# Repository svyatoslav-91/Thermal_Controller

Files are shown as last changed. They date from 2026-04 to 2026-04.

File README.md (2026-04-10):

Разработанное устройство (включая всю требуемую документацию согласно ЕСКД) — ПИД-регулятор контроля температуры печи оплавления с программируемым термопрофилем. 
Устройство снабжено преобразователем напряжения, подключающимся к бытовой электрической сети 230 В. Преобразователь питания снабжает энергией как цифровую часть устройства управления, так и аналоговую часть нагревательного устройства и устройства контроля температуры. 
Устройство имеет интерфейс взаимодействия с пользователем (ЖК-дисплей и клавиатурную панель). Также разработано ПО для управления, настройки и тестирования устройства с ПК на языке С. 
Цифровая часть управления реализована на микроконтроллере с ARM-архитектурой STM32F411CEU6 — микроконтроллер, 32-бит, Cortex-M4, 100 МГц, 512 КБ Flash, 128 КБ SRAM, 36 I/O [UFQFPN-48_7x7]. 
Аналоговые устройства взаимодействия с нагревательным элементом гальванически развязаны. Термопара в связке с MAX6675ISA по SPI передает данные о температуре в МК, который с помощью ПИД регуляции вычисляет необходимое время включения нагревателя в окне регулирования. 
Коммутирование нагревателя осуществляюется с помощью SSR реле что обеспечивает полную гальваническую развязку от цепи 220 В нагревателя, а также быстрый отклик.

По ссылке на видео размещена демонстрация работы устройства: программирование термопрофиля, запуск ПИД-регулятора, отображение температуры на ЖК-дисплее и в ПО на ПК, а также реакция системы на изменение уставки, запуск различных термопрофилей и запись во flash. (в качестве нагревателя для удобства используется лампочка накаливания).
(https://rutube.ru/video/9960f83b43a8872c07baa9010c9fd1d7/)

В корневой папке проекта можно найти:

принципиальные электрические схемы (в форматах PDFисходники для Altium Designer);

Gerber-файлы для изготовления печатной платы;

сборочные чертежи платы и корпуса (в форматах PDF);

спецификации компонентов (ВП, ПЭ3)(в форматах PDF);

3D-модель печатной платы (Step) для проверки совместимости с корпусом и механической интеграции;

исходные коды встроенного ПО для STM32F411CEU6 (с проектом для Keil);

исходный код ПО для ПК на языке C;

Вся конструкторская документация оформлена по стандартам ЕСКД (схемы, чертежи, спецификации, пояснительная записка). Проект полностью готов к серийному производству и может быть воспроизведён по предоставленным материалам.

В release-пакет включены:

исполняемый файл приложения для ПК (Windows) для управления, настройки и тестирования устройства;

краткое руководство пользователя (Release Notes).

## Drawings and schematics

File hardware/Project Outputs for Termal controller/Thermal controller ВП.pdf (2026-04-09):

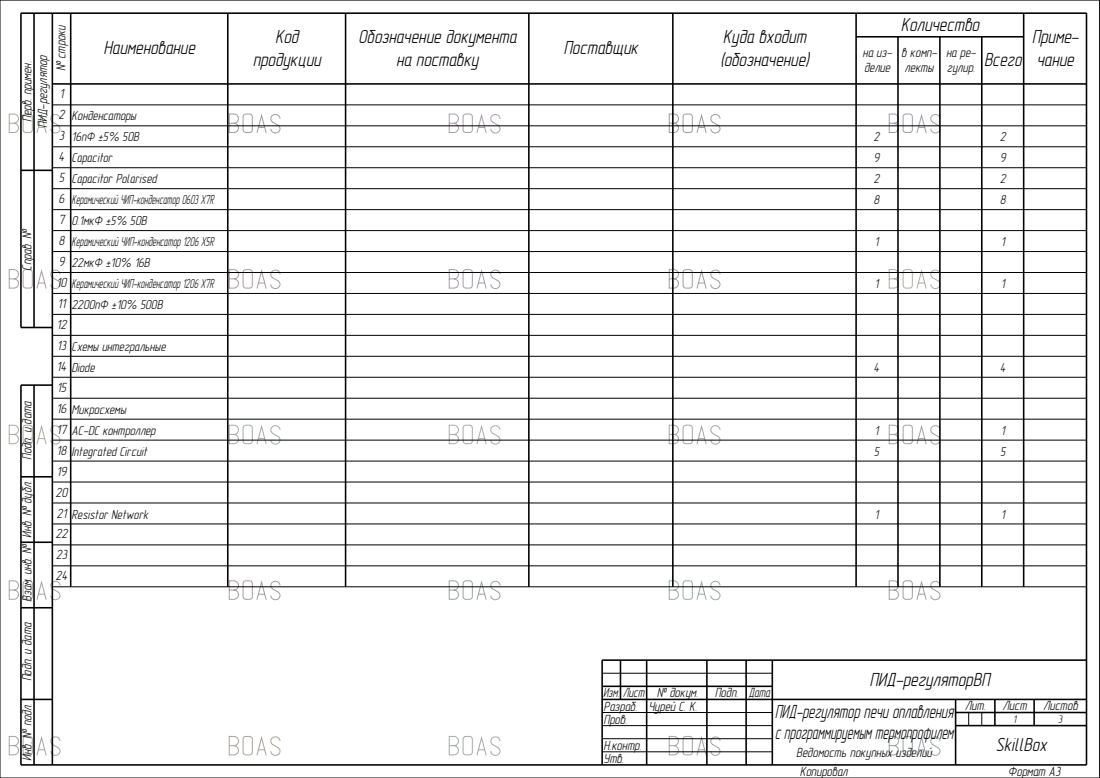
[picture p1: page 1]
Лит.; Копировал; Разраб. Пров.; Лист; Листов; Формат А3; Чурей С. К.; Ведомость покупных изделий; SkillBox; ПИД-регулятор

№ строки Наименование Код продукции Обозначение документа на поставку Поставщик Куда входит (обозначение) Количество на из- делие в комп- лекты на ре- гулир. Всего Приме- чание

Перв. примен. Справ. № Подп. и дата Инв. № дубл. Взам. инв. № Подп. и дата Инв. № подл.

2 | Конденсаторы
3 | 16пФ ±5% 50В | 2 | 2
4 | Capacitor | 9 | 9
5 | Capacitor Polarised | 2 | 2
6 | Керамический ЧИП-конденсатор 0603 X7R | 8 | 8
7 | 0.1мкФ ±5% 50В
8 | Керамический ЧИП-конденсатор 1206 X5R | 1 | 1
9 | 22мкФ ±10% 16В
10 | Керамический ЧИП-конденсатор 1206 X7R | 1 | 1
11 | 2200пФ ±10% 500В
12
13 | Схемы интегральные
14 | Diode | 4 | 4
15
16 | Микросхемы
17 | AC-DC контроллер | 1 | 1
18 | Integrated Circuit | 5 | 5
19
20
21 | Resistor Network | 1 | 1
22
23
24

ПИД-регуляторВП

Изм. Лист | № докум. | Подп. | Дата

ПИД-регулятор печи оплавления
с программируемым термопрофилем

Н.контр.
Утв.

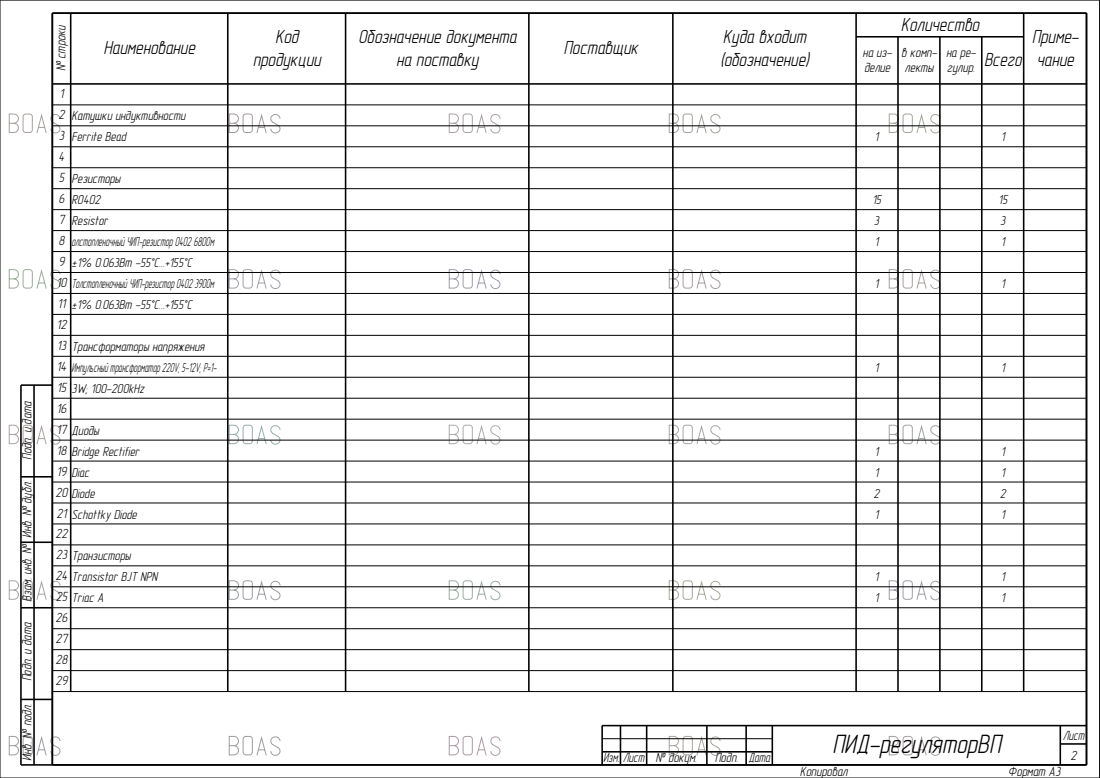
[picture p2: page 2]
Изм. Лист; № докум.; Подп.; Дата; Лист; ПИД-регуляторВП

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

2 | Катушки индуктивности
3 | Ferrite Bead | | 1 | 1
5 | Резисторы
6 | R0402 | | 15 | 15
7 | Resistor | | 3 | 3
8 | олстопленочный ЧИП-резистор 0402 680Ом | | 1 | 1
9 | ±1% 0.063Вт -55°С...+155°С
10 | Толстопленочный ЧИП-резистор 0402 390Ом | | 1 | 1
11 | ±1% 0.063Вт -55°С...+155°С
12
13 | Трансформаторы напряжения
14 | Импульсный трансформатор 220V; 5-12V; P=1- | | 1 | 1
15 | 3W; 100-200kHz
16
17 | Диоды
18 | Bridge Rectifier | | 1 | 1
19 | Diac | | 1 | 1
20 | Diode | | 2 | 2
21 | Schottky Diode | | 1 | 1
22
23 | Транзисторы
24 | Transistor BJT NPN | | 1 | 1
25 | Triac A | | 1 | 1
26
27
28
29

Подп. и дата Инв. № дубл. Взам. инв. № Подп. и дата Инв. № подл.

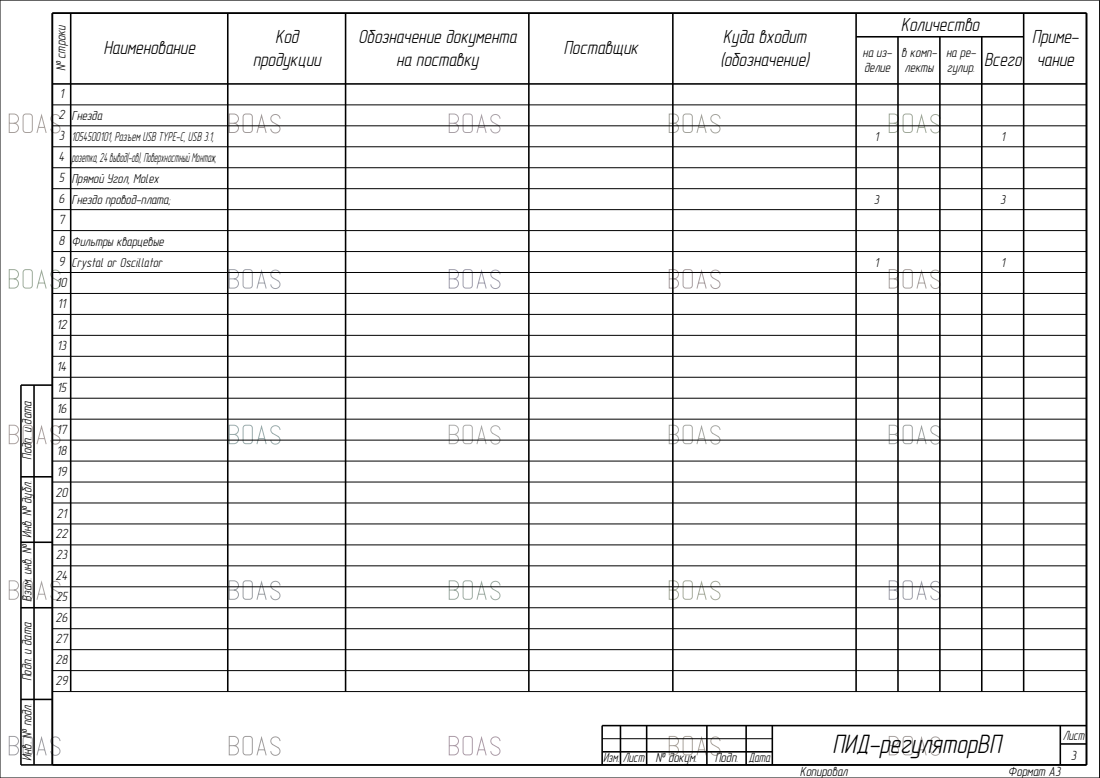
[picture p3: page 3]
Изм. Лист; № докум.; Подп.; Дата; Лист; ПИД-регуляторВП

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

2 | Гнезда
3 | 1054500101, Разъем USB TYPE-C, USB 3.1, | | 1 | 1
4 | розетка, 24 вывод(-ов), Поверхностный Монтаж,
5 | Прямой Угол, Molex
6 | Гнездо провод-плата; | | 3 | 3
8 | Фильтры кварцевые
9 | Crystal or Oscillator | | 1 | 1
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
Подп. и дата Инв. № дубл. Взам. инв. № Подп. и дата Инв. № подл.

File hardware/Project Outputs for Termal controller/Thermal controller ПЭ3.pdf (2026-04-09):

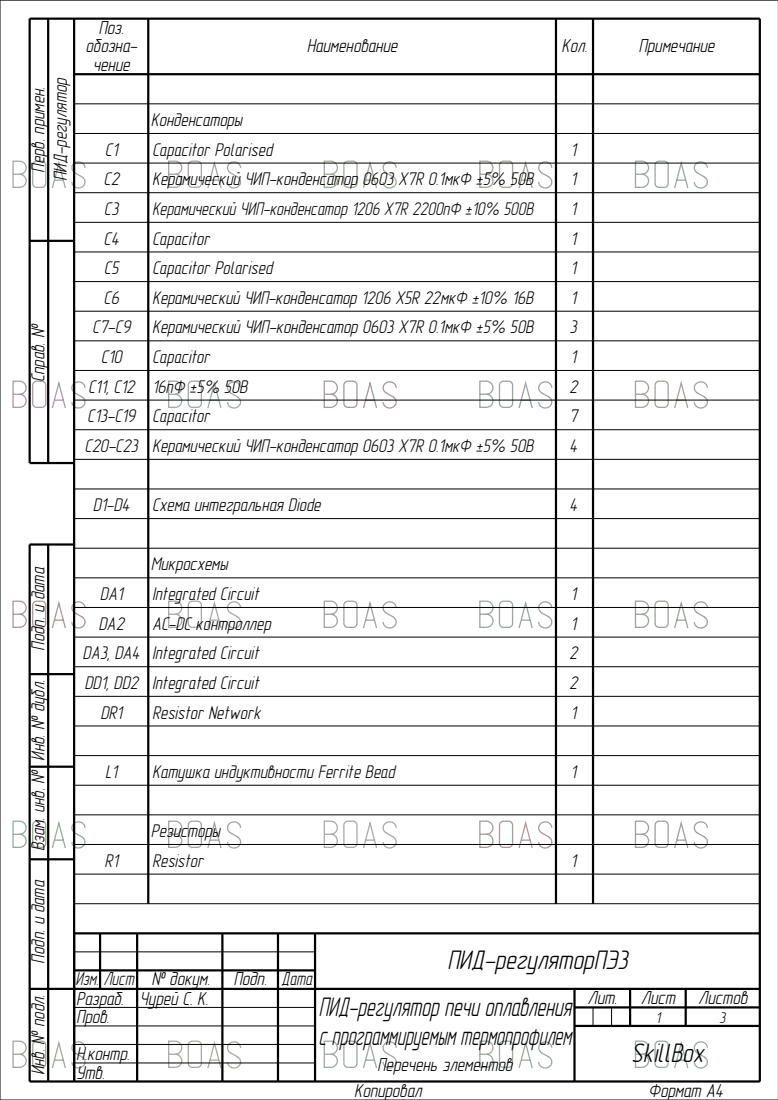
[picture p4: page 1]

Перв. примен. Справ. № Подп. и дата Инв. № дубл. Взам. инв. № Подп. и дата Инв. № подл.

Конденсаторы
C1 | Capacitor Polarised | 1
C2 | Керамический ЧИП-конденсатор 0603 X7R 0.1мкФ ±5% 50В | 1
C3 | Керамический ЧИП-конденсатор 1206 X7R 2200пФ ±10% 500В | 1
C4 | Capacitor | 1
C5 | Capacitor Polarised | 1
C6 | Керамический ЧИП-конденсатор 1206 X5R 22мкФ ±10% 16В | 1
C7-C9 | Керамический ЧИП-конденсатор 0603 X7R 0.1мкФ ±5% 50В | 3
C10 | Capacitor | 1
C11, C12 | 16пФ ±5% 50В | 2
C13-C19 | Capacitor | 7
C20-C23 | Керамический ЧИП-конденсатор 0603 X7R 0.1мкФ ±5% 50В | 4

Микросхемы
DA1 | Integrated Circuit | 1
DA2 | AC-DC контроллер | 1
DA3, DA4 | Integrated Circuit | 2
DD1, DD2 | Integrated Circuit | 2
DR1 | Resistor Network | 1

Резисторы
R1 | Resistor | 1

ПИД-регуляторПЭ3

Изм. Лист | № докум. | Подп. | Дата
Разраб. | Чурей С. К. | | ПИД-регулятор печи оплавления с программируемым термопрофилем Перечень элементов | Лит. | Лист | Листов
Пров.

Н.контр.
Утв.

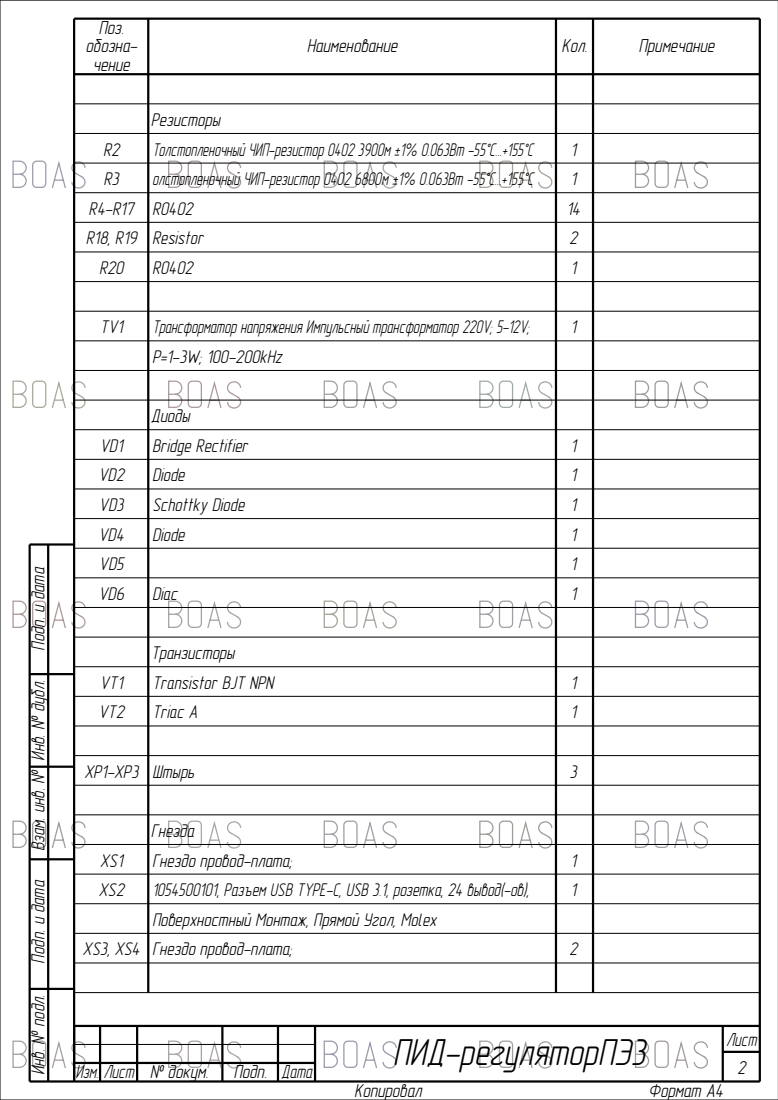
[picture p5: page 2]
Изм. Лист; № докум.; Подп.; Дата; Лист; ПИД-регуляторПЭ3; Штырь

Резисторы
R2 | Толстопленочный ЧИП-резистор 0402 390Ом ±1% 0.063Вт -55°С...+155°С | 1
R3 | олстопленочный ЧИП-резистор 0402 680Ом ±1% 0.063Вт -55°С...+155°С | 1
R4-R17 | R0402 | 14
R18, R19 | Resistor | 2
R20 | R0402 | 1

TV1 | Трансформатор напряжения Импульсный трансформатор 220V; 5-12V; | 1
P=1-3W; 100-200kHz

Диоды
VD1 | Bridge Rectifier | 1
VD2 | Diode | 1
VD3 | Schottky Diode | 1
VD4 | Diode | 1
VD5 | | 1
VD6 | Diac | 1

Подп. и дата Инв. № дубл. Взам. инв. № Подп. и дата Инв. № подл.

Транзисторы
VT1 | Transistor BJT NPN | 1
VT2 | Triac A | 1

Гнезда
XS1 | Гнездо провод-плата; | 1
XS2 | 1054500101, Разъем USB TYPE-C, USB 3.1, розетка, 24 вывод(-ов), | 1
Поверхностный Монтаж, Прямой Угол, Molex

XS3, XS4 | Гнездо провод-плата; | 2

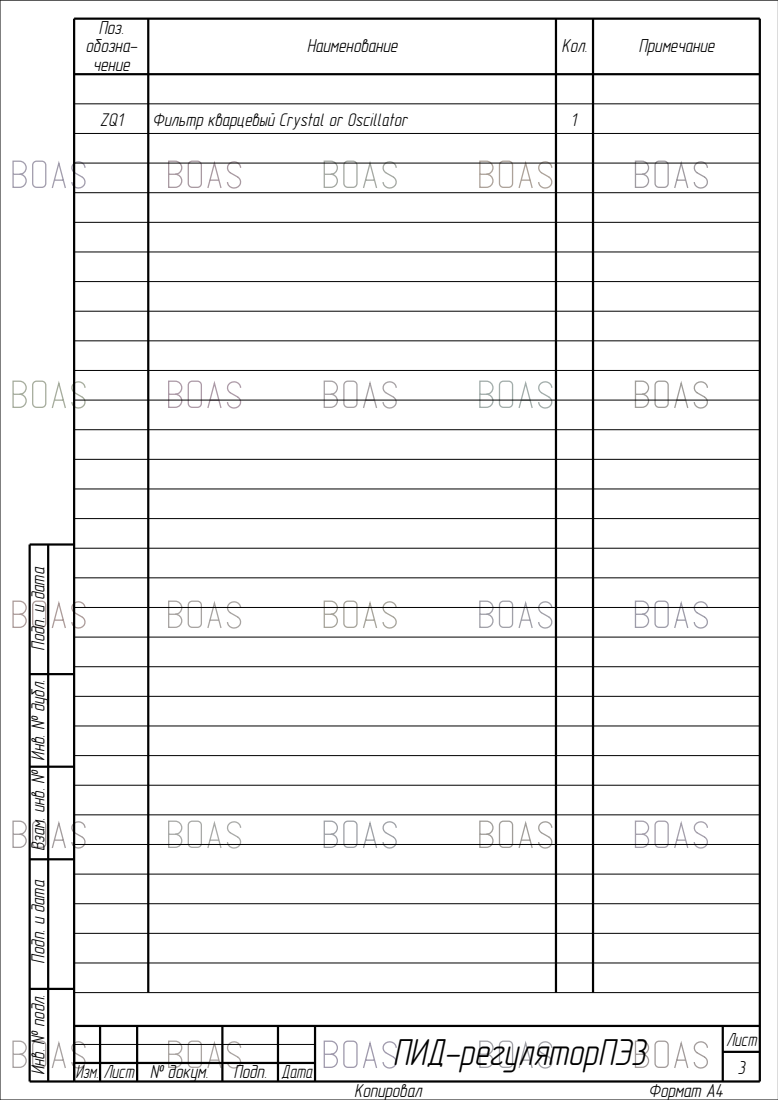
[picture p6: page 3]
Изм. Лист; № докум.; Подп.; Дата; Лист; ПИД-регуляторПЭ3; Фильтр кварцевый Crystal or Oscillator

Подп. и дата Инв. № дубл. Взам. инв. № Подп. и дата Инв. № подл.

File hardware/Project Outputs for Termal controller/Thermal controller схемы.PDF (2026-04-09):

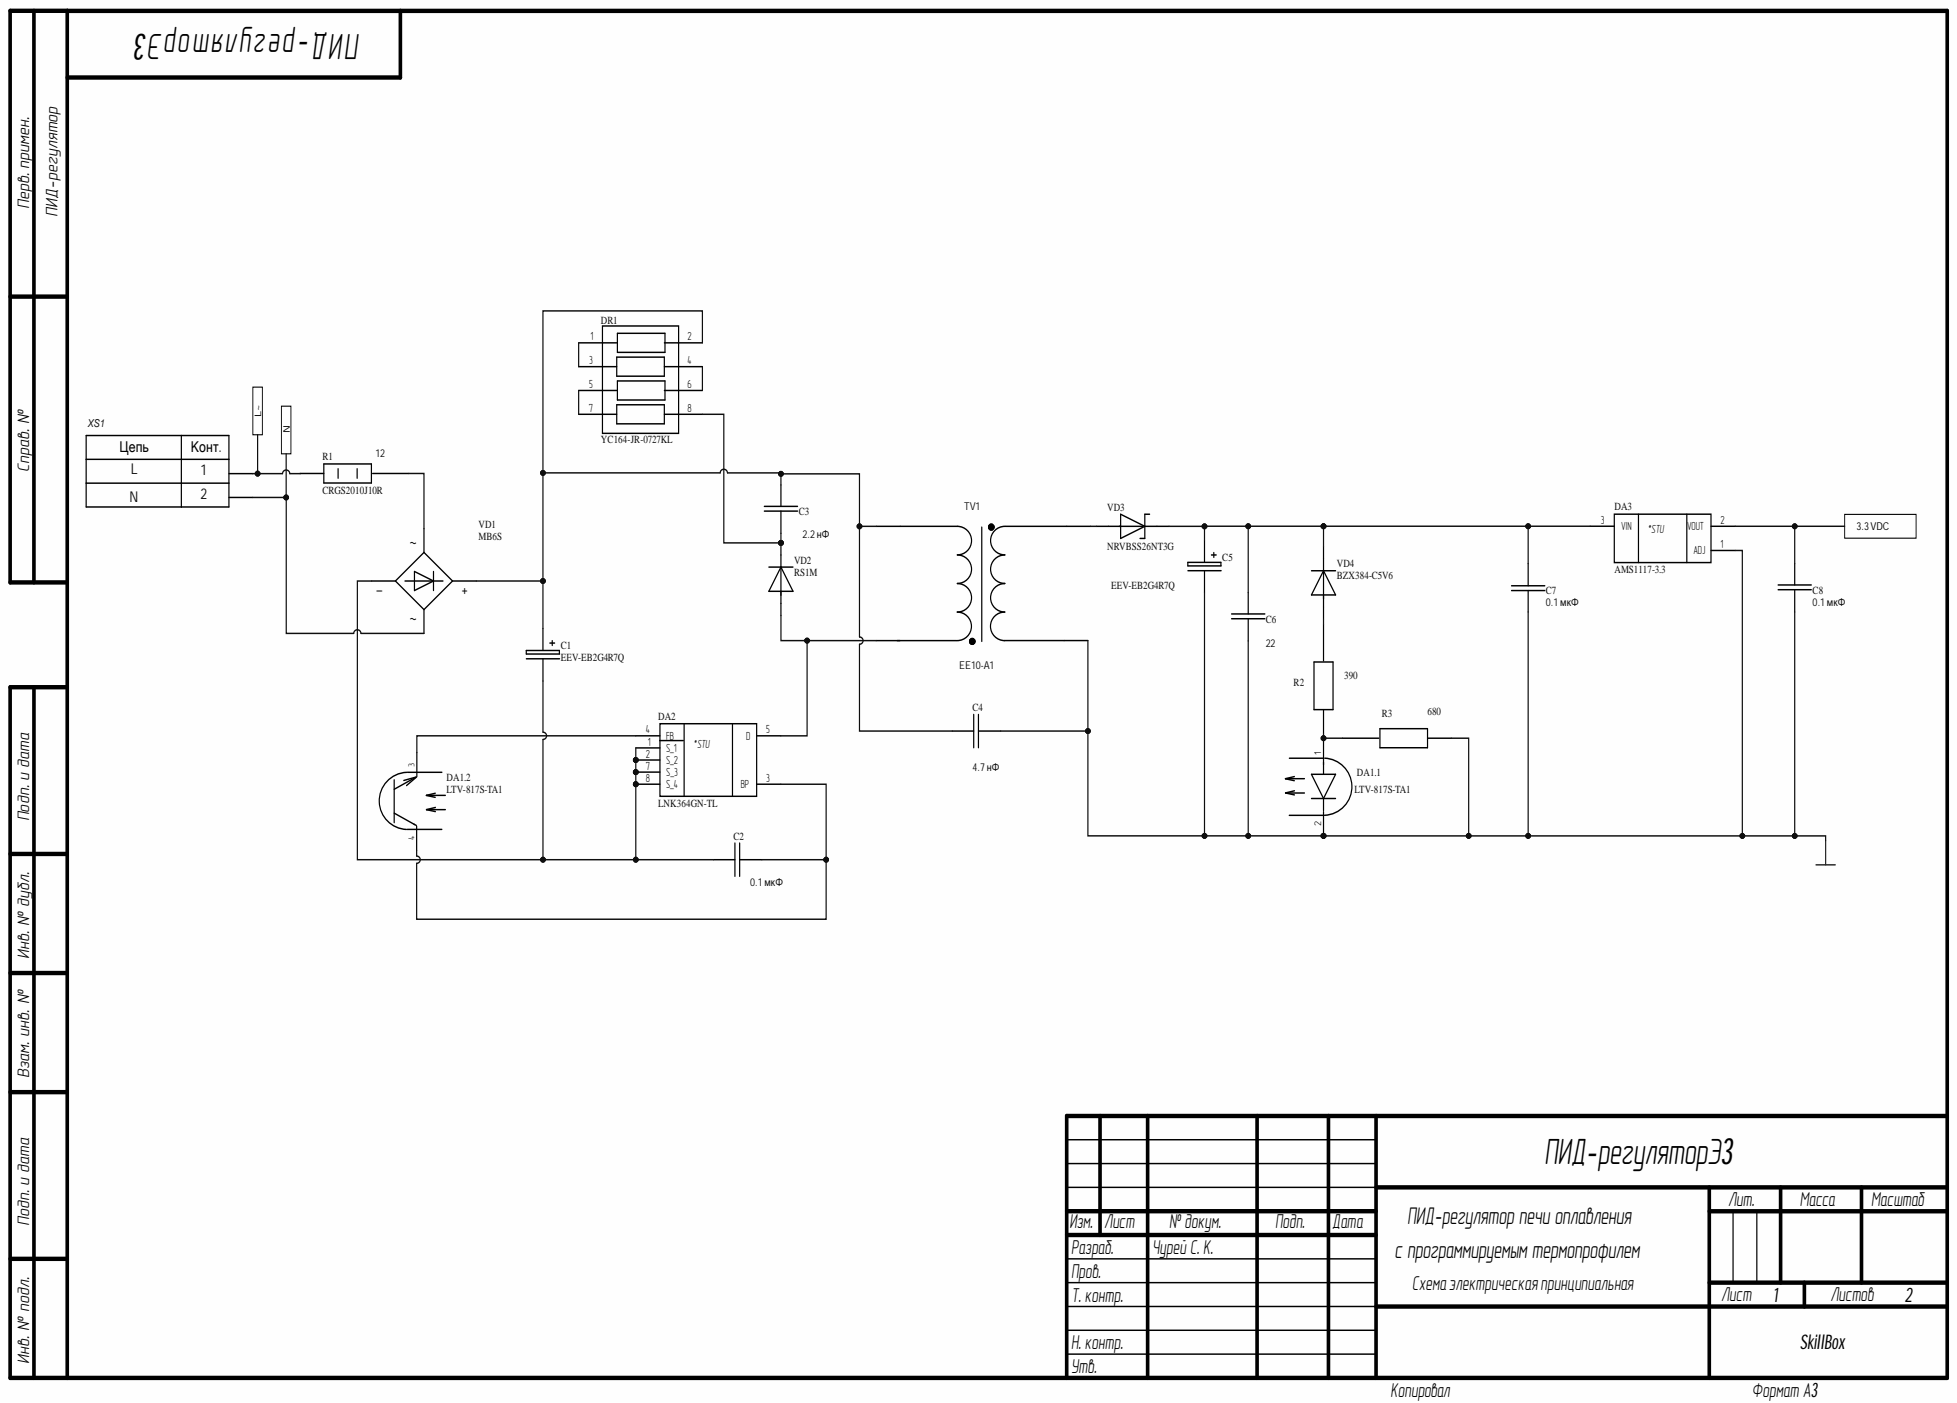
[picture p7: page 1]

Инв. № подл. Подп. и дата Инв. № дубл. Подп. и дата Взам. инв. № Перв. примен. Справ. №

ПИД -регуляторЭ 3

ПИД -регулятор печи оплавления с программируемым термопрофилем С х ема э л е ктр и ч е с к ая пр и нци п и ал ь н ая | Лит . | Мас с а | Масшт аб

Изм . | Лис т | № до к у м . | Подп . | Дата
Разр аб . | | Чур е й С. К .
Про в .
Т. к о нтр . | | | | | Лис т 1 | Листо в 2

Н. к о нтр .
Утв .

SkillBox

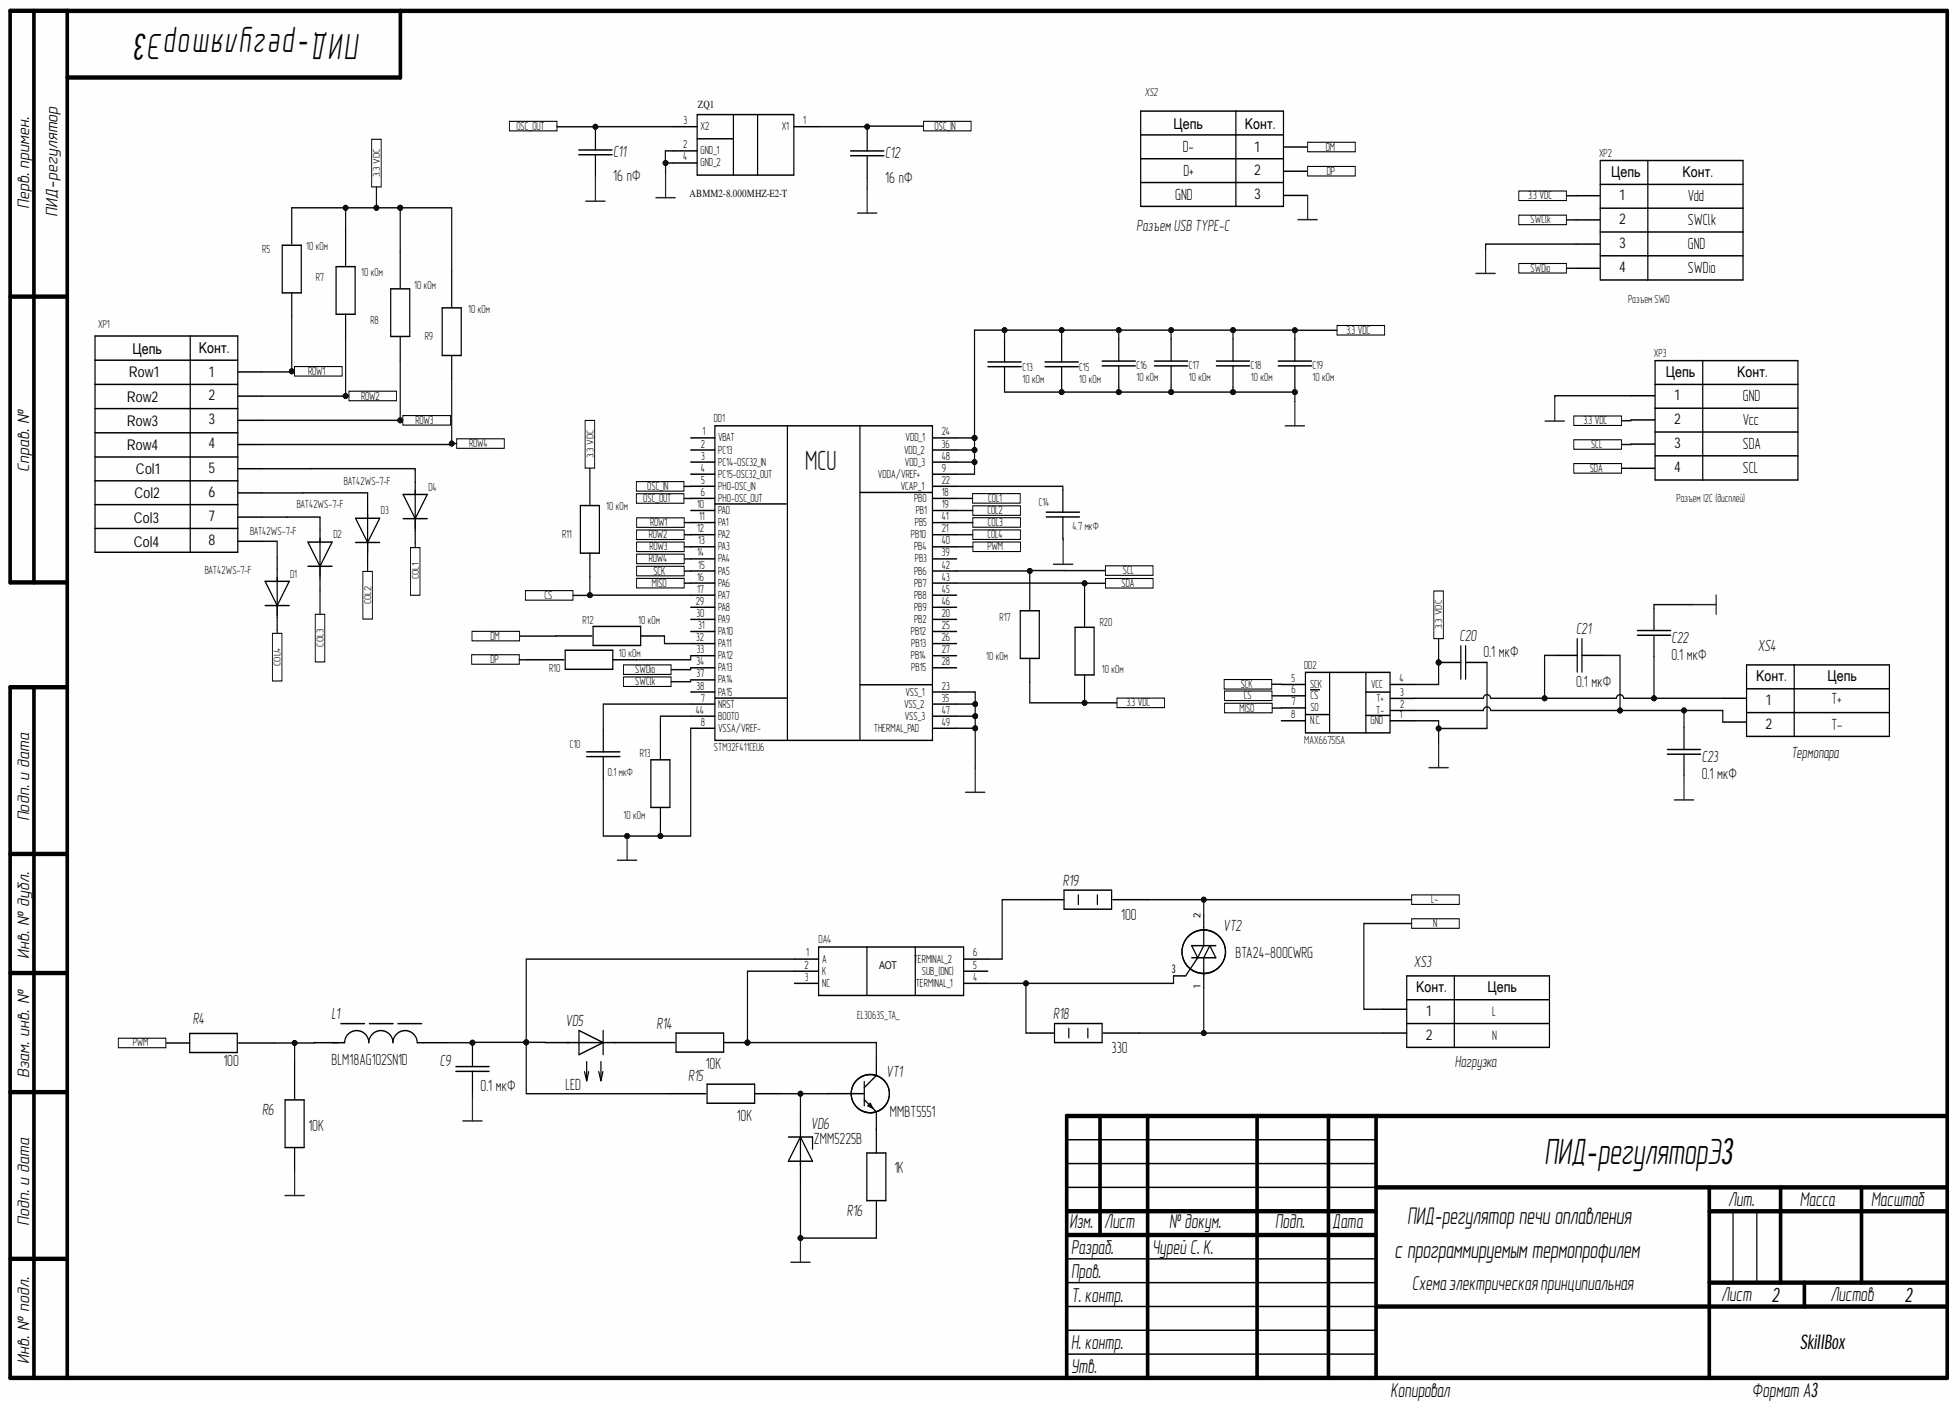
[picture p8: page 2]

Цепь | Конт.
D- | 1

2 | SWClk
3 | GND
4 | SWDio

Конт. | Цепь

LED

Изм. | Лист | № докум. | Подп. | Дата
Разраб. | | Чурей С. К.
Пров.
Т. контр. | | | | | Лист 2 | Листов 2

ПИД-регулятор печи оплавления
с программируемым термопрофилем
Схемаэлектрическаяпринципиальная

Н. контр.
Утв.

SkillBox

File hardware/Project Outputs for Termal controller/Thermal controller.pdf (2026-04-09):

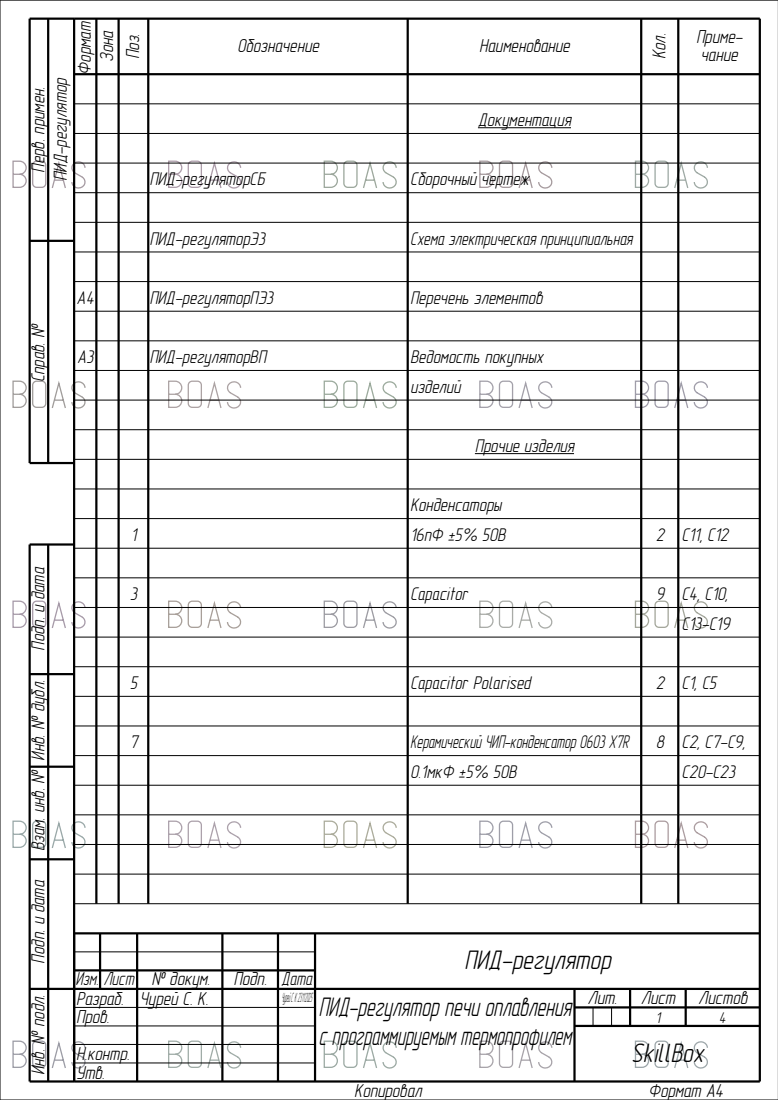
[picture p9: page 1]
Копировал; Формат А4; SkillBox; ПИД-регулятор; Формат; Зона; Поз.; Обозначение; Наименование; Кол.; Приме- чание; Документация; ПИД-регуляторСБ; Сборочный чертеж; ПИД-регуляторЭ3; Схема электрическая принципиальная; ПИД-регуляторПЭ3; Перечень элементов; Прочие изделия; Capacitor Polarised

Перв. примен. Справ. № Подп. и дата Инв. № дубл. Взам. инв. № Подп. и дата Инв. № подл.

А3 | ПИД-регуляторВП | Ведомость покупных

изделий

Конденсаторы

3 | Capacitor | 9 | C4, C10,

7 | Керамический ЧИП-конденсатор 0603 X7R | 8 | C2, C7-C9,

0.1мкФ ±5% 50В | | C20-C23

ПИД-регулятор

Изм. Лист | № докум. | Подп. | Дата
Разраб. | Чурей С. К. | | Чурей С. К. 23.11.2025 | ПИД-регулятор печи оплавления с программируемым термопрофилем | Лит. | Лист | Листов
Пров.

Н.контр.
Утв.

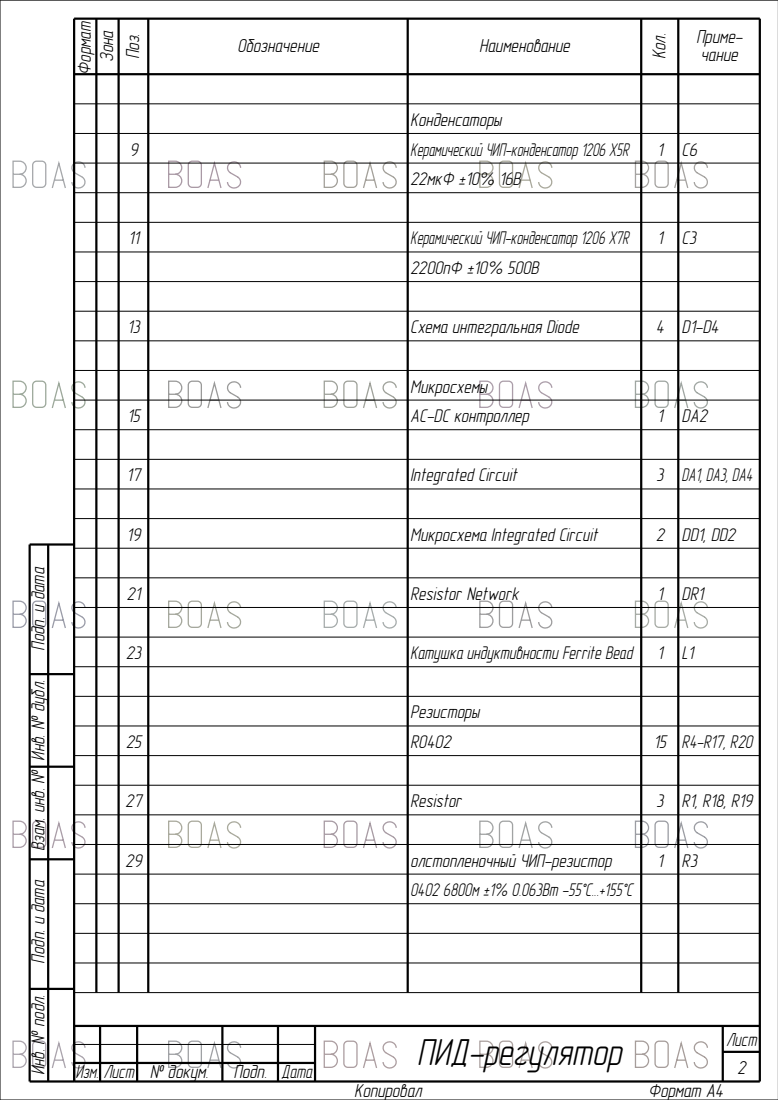
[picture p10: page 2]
Изм. Лист; № докум.; Подп.; Дата; Лист; ПИД-регулятор; Схема интегральная Diode; Integrated Circuit; Микросхема Integrated Circuit; Resistor Network; Катушка индуктивности Ferrite Bead; Resistor

Конденсаторы

9 | Керамический ЧИП-конденсатор 1206 X5R | 1 | C6

22мкФ ±10% 16В

11 | Керамический ЧИП-конденсатор 1206 X7R | 1 | C3

Микросхемы

15 | AC-DC контроллер | 1 | DA2

Подп. и дата Инв. № дубл. Взам. инв. № Подп. и дата Инв. № подл.

Резисторы

29 | олстопленочный ЧИП-резистор | 1 | R3

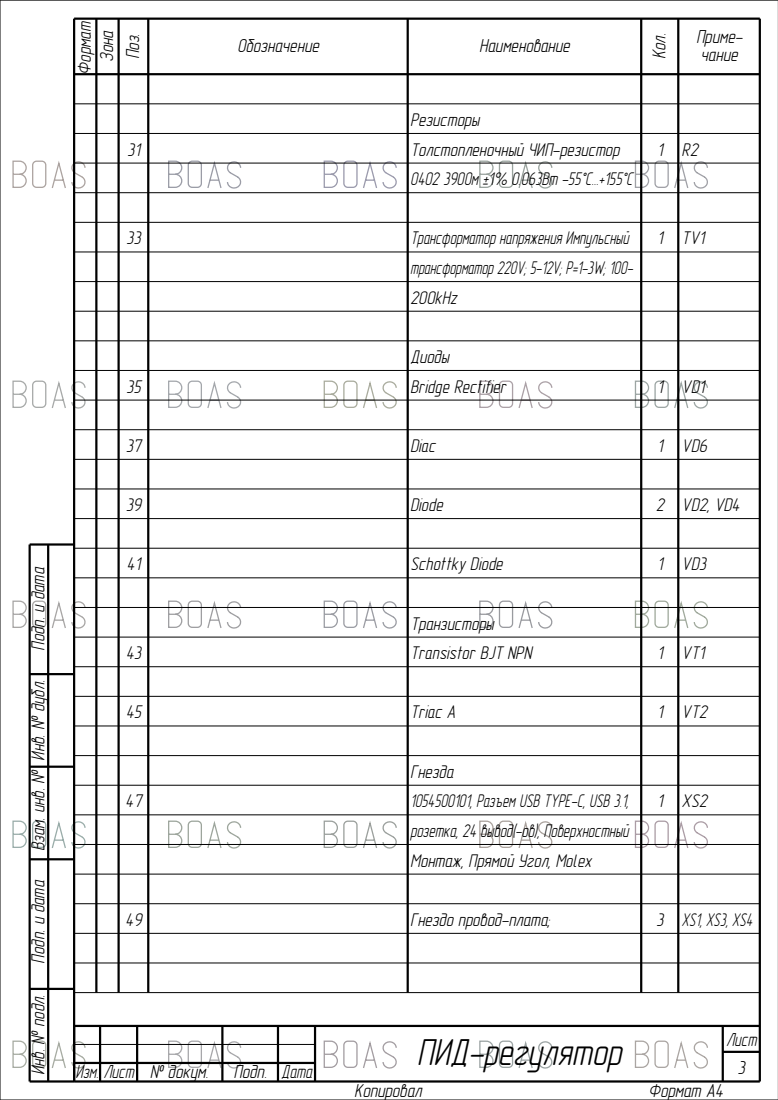
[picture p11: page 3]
Diac; Diode; Schottky Diode; Triac A; Гнездо провод-плата;

Резисторы

31 | Толстопленочный ЧИП-резистор | 1 | R2

33 | Трансформатор напряжения Импульсный | 1 | TV1

трансформатор 220V; 5-12V; P=1-3W; 100-
200kHz

Диоды

35 | Bridge Rectifier | 1 | VD1

Подп. и дата Инв. № дубл. Взам. инв. № Подп. и дата Инв. № подл.

Транзисторы

43 | Transistor BJT NPN | 1 | VT1

Гнезда

47 | 1054500101, Разъем USB TYPE-C, USB 3.1, | 1 | XS2

розетка, 24 вывод(-ов), Поверхностный
Монтаж, Прямой Угол, Molex

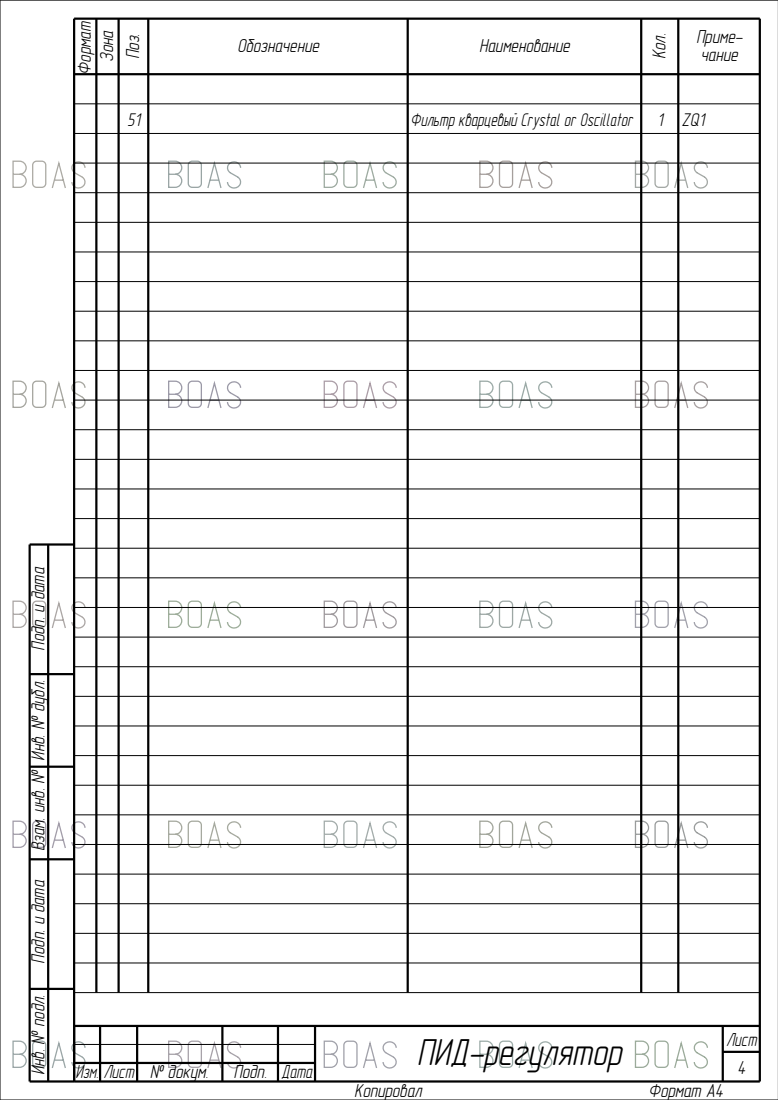
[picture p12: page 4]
Фильтр кварцевый Crystal or Oscillator

Подп. и дата Инв. № дубл. Взам. инв. № Подп. и дата Инв. № подл.



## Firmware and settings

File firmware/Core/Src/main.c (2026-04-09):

#include <stdlib.h>
#include <math.h>
#include "main.h"
#include "gpio.h"
#include "i2c1.h"
#include "spi1.h"
#include "tim.h"
#include "pid_controller.h"
#include "flash.h"
#include "idwg.h"
#include "usb_device.h"
#include "usbd_cdc_if.h"
#include "MAX6675.h"
#include "LCD20x4.h"
#include "Keypad4x4.h"
#include "PC_program_commands.h"

const char* startup_msg = "\r\nReflow Controller Ready\r\n";

volatile SystemState_t current_state = STATE_IDLE;
SystemState_t previous_state = STATE_IDLE;

// Буферы для USB коммуникации

volatile uint8_t usb_rx_buffer[USB_RX_BUFFER_SIZE] = {0};
volatile uint8_t usb_rx_len = 0;
char usb_tx_buffer[USB_TX_BUFFER_SIZE] = {0};

// Флаги и переменны для расчета ПИД
float setpoint_temp = 30.0f;
static uint16_t on_steps = 0;
static uint16_t tim3_counter = 0;
static uint8_t need_new_pid_calc = 0;

// Буфер усреднения температуры
static float temp_buffer[5] = {0};
static uint8_t temp_index = 0;
static uint8_t temp_count = 0;

float temp_raw = 0.0f;     // Последнее измерение MAX6675
float temp_avg = 0.0f;     // Усреднённая температура

volatile uint8_t temp_read_needed = 0;
volatile uint8_t temp_ready = 0;   // Становится 1 когда набрано 5 измерений

void add_temperature_sample(float t)
{
    temp_buffer[temp_index] = t;
    temp_index = (temp_index + 1) % 3;

    if (temp_count < 3) temp_count++;

    if (temp_count == 3)
    {
        float sum = 0.0f;
        for (uint8_t i = 0; i < 3; i++) sum += temp_buffer[i];

        temp_avg = sum / 3.0f;
        temp_ready = 1;
    }
    else
    {
        temp_ready = 0;
    }
}

void SysTick_Handler(void)
{
  HAL_IncTick();
}

void TIM3_IRQHandler(void)
{
  HAL_TIM_IRQHandler(&htim3);
}

void OTG_FS_IRQHandler(void)
{

  HAL_PCD_IRQHandler(&hpcd_USB_OTG_FS);

}
// Обновление уставки по профилю
void update_profile_setpoint(void)
{
    if (!profile_running || profile_point_count == 0) return;
    
    float elapsed_time = (HAL_GetTick() - profile_start_time) / 1000.0f; // в секундах
	
    // Если вышли за последнюю точку — ставим на последнюю
    if (elapsed_time >= (uint32_t)temperature_profile[profile_point_count - 1].time_sec) {
        current_profile_point = profile_point_count - 1;
        setpoint_temp = temperature_profile[current_profile_point].temperature;
        stop_profile();
        return;
    }
	  // Проверяем, чтобы current_profile_point не вылез за границы
    if (current_profile_point >= profile_point_count) current_profile_point = profile_point_count - 1;
    
    // Находим текущую точку профиля
    while (current_profile_point < profile_point_count - 1 &&
			     elapsed_time >= temperature_profile[current_profile_point + 1].time_sec) current_profile_point++; 
    
    // Интерполяция между точками
    if (current_profile_point < profile_point_count - 1) 
		{
        float t1 = temperature_profile[current_profile_point].time_sec;
        float t2 = temperature_profile[current_profile_point + 1].time_sec;
        float temp1 = temperature_profile[current_profile_point].temperature;
        float temp2 = temperature_profile[current_profile_point + 1].temperature;

        if (t2 > t1) {
            float ratio = (elapsed_time - t1) / (t2 - t1);
            setpoint_temp = temp1 + (temp2 - temp1) * ratio;
        } else setpoint_temp = temp1;

    } 
		else setpoint_temp = temperature_profile[profile_point_count - 1].temperature;
     // Если профиль завершен
    if (elapsed_time >= temperature_profile[profile_point_count - 1].time_sec) {
        stop_profile();
    }
}

void HAL_TIM_PeriodElapsedCallback(TIM_HandleTypeDef *htim)
{
	if (htim->Instance == TIM3)
	{   
		  static uint32_t temp_timer = 0;
      temp_timer++;
        
      if (temp_timer >= 20) 
		  {  // Устанавливаем флаг каждые 200 мс
          temp_timer = 0;
          temp_read_needed = 1;
				
      }
				
		  static uint32_t pid_control_counter = 0;
		  pid_control_counter++;
		
		  if (pid_control_counter >= pid_calls_countaty) 
		  {
          pid_control_counter = 0;  
          need_new_pid_calc = 1;
      }
      // Управление счетчиком ШИМ
      static uint16_t local_tim3_counter = 0;
      local_tim3_counter++;
      if (local_tim3_counter >= steps_in_window) 
			{
          local_tim3_counter = 0;
      }
      tim3_counter = local_tim3_counter;  // Копируем в общую переменную
			
			// Обновление уставки по профилю
      if (profile_running && current_state == STATE_RUNNING_PROFILE) 
			{
          static uint32_t last_profile_update = 0;
          uint32_t current_time = HAL_GetTick();
          if (current_time - last_profile_update >= 1000) 
					{ // Обновляем каждую секунду
              last_profile_update = current_time;
              profile_update_needed = 1;
          }
      }
	 }
}

int main(void)
{
  HAL_Init();
	
  SystemClock_Config();
	
  GPIO_Init();
	TIM3_Init();
  I2C1_Init();
  SPI1_Init();
	USB_DEVICE_Init();
	IWDG_Init();
  LCD_Init();
	
	// Иниализируем ПИД контроллер стандартными значениями
	PID_Standart_Init (&heater);

	// Загружаем PID коэффициенты
	Flash_Read_PIDCoef_Storage(&heater);
	
  if (isnan(heater.Kp) || isnan(heater.Ki) || isnan(heater.Kd)) 
	{
    PID_Standart_Init (&heater);
  }
		// Загружаем сохраненный профиль
  Flash_Read_Profile_Storage(&flash_profile);
	
  Flash_Profile_Init(temperature_profile);
			
	CDC_Transmit_FS((uint8_t*)startup_msg, strlen(startup_msg));
  HAL_Delay(10);  // Дать время на отправку
	
	LCD_Clear();
	LCD_SetCursor(0, 0);
	LCD_PrintString("System Ready");
  HAL_Delay(1000);

  while (1)
  {	
		// Чтение температуры по флагу из прерывания
    if (temp_read_needed) {
        temp_read_needed = 0;
			  read_max6675();
			  temp_raw = temp;      // копируем для ясности
        add_temperature_sample(temp_raw);
    }
		//Обработка команд с клавиатуры
		char key = read_keypad();
		process_keypress(key);
		//Обработка команд от программы
		if (cmd_ready) 
		{
    cmd_ready = 0;
    process_usb_command(pending_cmd);
    }
		
		// Сброс ПИД при смене состояния
    if (previous_state != current_state) {
        PID_Clear(&heater);
        previous_state = current_state;  // Обновляем предыдущее состояние
    }
		   
		    if (current_state == STATE_IDLE)
		    {
			      //LCD_Clear();
					  HAL_GPIO_WritePin(TPC_GPIO_Port,TPC_Pin, GPIO_PIN_RESET);
	          LCD_SetCursor(0, 0);
	          LCD_PrintString("'A' to set temp");
			      LCD_SetCursor(0, 2);
	          LCD_PrintString("'D' to start profile");
					  LCD_SetCursor(0, 3);
					  float displayed_temp = temp_avg;
  				  snprintf(lcd_buffer, sizeof(lcd_buffer), "Temp:%.1fC", displayed_temp);
  					LCD_PrintString(lcd_buffer);
		    }
				
			  if (current_state == STATE_RUNNING_SETPOINT || current_state == STATE_RUNNING_PROFILE)
		    {	
			      //static uint16_t last_tim3_counter = 0;
	          static uint8_t power_percentage = 0;
			      if (profile_update_needed) 
						{
                profile_update_needed = 0;
                update_profile_setpoint();
            }
		        if (need_new_pid_calc == 1) 
		        {
                need_new_pid_calc = 0;
													
                float current_temp = temp_avg;
            			
                if (temp_ready) 
						    {
                    float pid_output = PID_Calculate(&heater, setpoint_temp, current_temp, dt);
                    power_percentage = (uint8_t)pid_output;
                }	
					  }
						else power_percentage = 0; // Пока нет 5 измерений - отключаем нагрев или используем минимальную мощность

            on_steps = (power_percentage * steps_in_window)/100;  
		
		        if (tim3_counter < on_steps) 
		   			{ 
		            HAL_GPIO_WritePin(TPC_GPIO_Port,TPC_Pin, GPIO_PIN_SET);
			          HAL_GPIO_TogglePin(GPIOC, GPIO_PIN_13);
		        }
		        else 
		        {
		            HAL_GPIO_WritePin(TPC_GPIO_Port,TPC_Pin, GPIO_PIN_RESET);
			          HAL_GPIO_TogglePin(GPIOC, GPIO_PIN_13);
		        }
												
             if (current_state == STATE_RUNNING_SETPOINT)
						 {
		             LCD_SetCursor(0, 0);
							   snprintf(lcd_buffer, sizeof(lcd_buffer), "Set_temp:%.1fC", setpoint_temp);
  							 LCD_PrintString(lcd_buffer);
							 
							   float displayed_temp;
							   if(temp_ready) displayed_temp = temp_avg;
  							 LCD_SetCursor(0, 1);
  							 snprintf(lcd_buffer, sizeof(lcd_buffer), "Temp:%.1fC", displayed_temp);
  							 LCD_PrintString(lcd_buffer);
		
							   LCD_SetCursor(0, 2);
							 	 snprintf(lcd_buffer, sizeof(lcd_buffer), "PWR:%2d%% CNT:%4d", power_percentage, tim3_counter);
  							 LCD_PrintString(lcd_buffer);

							 	 LCD_SetCursor(0, 3);  
  							 snprintf(lcd_buffer, sizeof(lcd_buffer), "ON:%4d/%4d", on_steps, steps_in_window);
  							 LCD_PrintString(lcd_buffer);
						 }
						 if (current_state == STATE_RUNNING_PROFILE)
						 {
						     LCD_SetCursor(0, 0);
  							 snprintf(lcd_buffer, sizeof(lcd_buffer), "Point:%d", current_profile_point);
							   LCD_PrintString(lcd_buffer);
						
							   float displayed_temp;
							   if(temp_ready) displayed_temp = temp_avg;
							   LCD_SetCursor(0, 1);
							   snprintf(lcd_buffer, sizeof(lcd_buffer), "Temp:%.1fC", displayed_temp);
							   LCD_PrintString(lcd_buffer);
		
				         LCD_SetCursor(0, 2);
							   uint32_t current_profile_time = (HAL_GetTick() - profile_start_time)/1000;
							   snprintf(lcd_buffer, sizeof(lcd_buffer), "CurTime:%d",current_profile_time);
							   LCD_PrintString(lcd_buffer);

						     LCD_SetCursor(0, 3);  
						     snprintf(lcd_buffer, sizeof(lcd_buffer), "Spoint:%.1fC ", setpoint_temp);
						     LCD_PrintString(lcd_buffer);
						 }
	     }
		HAL_IWDG_Refresh(&hiwdg);
   } 
}


void SystemClock_Config(void)
{
  RCC_OscInitTypeDef RCC_OscInitStruct = {0};
  RCC_ClkInitTypeDef RCC_ClkInitStruct = {0};

  __HAL_RCC_PWR_CLK_ENABLE();
  __HAL_PWR_VOLTAGESCALING_CONFIG(PWR_REGULATOR_VOLTAGE_SCALE1);

  RCC_OscInitStruct.OscillatorType = RCC_OSCILLATORTYPE_LSI|RCC_OSCILLATORTYPE_HSE;
  RCC_OscInitStruct.HSEState = RCC_HSE_ON;
  RCC_OscInitStruct.LSIState = RCC_LSI_ON;
  RCC_OscInitStruct.PLL.PLLState = RCC_PLL_ON;
  RCC_OscInitStruct.PLL.PLLSource = RCC_PLLSOURCE_HSE;
  RCC_OscInitStruct.PLL.PLLM = 25;
  RCC_OscInitStruct.PLL.PLLN = 192;
  RCC_OscInitStruct.PLL.PLLP = RCC_PLLP_DIV2;
  RCC_OscInitStruct.PLL.PLLQ = 4;
  if (HAL_RCC_OscConfig(&RCC_OscInitStruct) != HAL_OK)
  {
    Error_Handler();
  }

  RCC_ClkInitStruct.ClockType = RCC_CLOCKTYPE_HCLK|RCC_CLOCKTYPE_SYSCLK
                              |RCC_CLOCKTYPE_PCLK1|RCC_CLOCKTYPE_PCLK2;
  RCC_ClkInitStruct.SYSCLKSource = RCC_SYSCLKSOURCE_PLLCLK;
  RCC_ClkInitStruct.AHBCLKDivider = RCC_SYSCLK_DIV1;
  RCC_ClkInitStruct.APB1CLKDivider = RCC_HCLK_DIV2;
  RCC_ClkInitStruct.APB2CLKDivider = RCC_HCLK_DIV1;

  if (HAL_RCC_ClockConfig(&RCC_ClkInitStruct, FLASH_LATENCY_3) != HAL_OK)
  {
    Error_Handler();
  }
}


void Error_Handler(void)
{

  __disable_irq();
  while (1)
  {
		HAL_GPIO_TogglePin(GPIOC, GPIO_PIN_13);
		HAL_Delay(100);
  }

}

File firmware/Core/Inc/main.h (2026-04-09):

#pragma once 
#include "stm32f4xx_hal.h"
#include "pid_controller.h"

#define Row1_Pin GPIO_PIN_1
#define Row1_GPIO_Port GPIOA
#define Row2_Pin GPIO_PIN_2
#define Row2_GPIO_Port GPIOA
#define Row3_Pin GPIO_PIN_3
#define Row3_GPIO_Port GPIOA
#define Row4_Pin GPIO_PIN_4
#define Row4_GPIO_Port GPIOA
#define CS_MAX6675_Pin GPIO_PIN_7
#define CS_MAX6675_GPIO_Port GPIOA
#define Col1_Pin GPIO_PIN_0
#define Col1_GPIO_Port GPIOB
#define Col2_Pin GPIO_PIN_1
#define Col2_GPIO_Port GPIOB
#define Col3_Pin GPIO_PIN_5
#define Col3_GPIO_Port GPIOB
#define Col4_Pin GPIO_PIN_10
#define Col4_GPIO_Port GPIOB
#define TPC_GPIO_Port GPIOB
#define TPC_Pin GPIO_PIN_4

#define USB_RX_BUFFER_SIZE 64
#define USB_TX_BUFFER_SIZE 64

#define CMD_BUF_SIZE 128

#define MAX_PROFILE_POINTS 50

typedef enum {
    STATE_IDLE,
	  STATE_SET_TEMP,
	  STATE_RUNNING_SETPOINT,
    STATE_RUNNING_PROFILE
} SystemState_t;

extern PCD_HandleTypeDef hpcd_USB_OTG_FS;
extern volatile uint8_t usb_rx_buffer[USB_RX_BUFFER_SIZE];
extern volatile uint8_t usb_rx_len;
extern float setpoint_temp;
extern volatile SystemState_t current_state;

extern char usb_tx_buffer[USB_TX_BUFFER_SIZE];
extern volatile uint16_t window_time_ms;
extern float setpoint_temp;
extern float temp_avg; 
extern volatile uint8_t temp_ready; 

void SystemClock_Config(void);
void Error_Handler(void);
void process_usb_command(char* command);
void update_profile_setpoint(void);



typedef struct {
    float time_sec;
    float temperature;
} ProfilePoint_t;

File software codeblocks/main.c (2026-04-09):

#include <gtk/gtk.h>
#include <windows.h>
#include <locale.h>
#include <string.h>
#include <stdlib.h>
#include <stdio.h>
#include <math.h>  // Для M_PI и математических функций

/* ---------- Конфигурация ---------- */
#define GET_STATUS_POLL_MS 300  /* опрашивать телеметрию каждые 300 ms */
#define MAX_LOG_LINES 1000

/* ---------- список точек (time_sec, temp_C) ---------- */
typedef struct {
    double t; /* seconds */
    double temp; /* °C */
} ProfilePoint;

typedef struct {
    ProfilePoint *pts;
    size_t count;
    size_t cap;
} Profile;

/* ---------- Real-time data logging ---------- */
typedef struct {
    double time;    // время в секундах
    double temp;    // температура
    double setpoint; // заданная температура
} RealtimePoint;

typedef struct {
    RealtimePoint *points;
    size_t count;
    size_t capacity;
    guint start_time; // время начала записи в мс
    gboolean recording;
} RealtimeData;

static RealtimeData realtime_data;
static gboolean profile_draw(GtkWidget *widget, cairo_t *cr, gpointer data);
static void draw_axes(cairo_t *cr, int w, int h, double tmin, double tmax, double tempmin, double tempmax);
static void process_received_data(const char *data);
static void on_get_profile(GtkButton *b, gpointer user_data);
static gboolean update_profile_time_cb(gpointer data);
static gboolean disable_serial_logging(gpointer data);
static void stop_periodic_telemetry(void);
static void start_periodic_telemetry(void);
static void realtime_data_add(RealtimeData *rd, double temp, double setpoint);
static void realtime_data_start(RealtimeData *rd);
static void realtime_data_stop(RealtimeData *rd);
static void realtime_data_clear(RealtimeData *rd);
static void realtime_data_init(RealtimeData *rd);
static void realtime_data_free(RealtimeData *rd);
static void fill_table_from_profile(void);
static void draw_legend(cairo_t *cr, int w, int h, gboolean draw_profile, gboolean draw_realtime);

static void profile_init(Profile *p) {
    p->pts = NULL; p->count = 0; p->cap = 0;
}
static void profile_free(Profile *p) { free(p->pts); p->pts = NULL; p->count = p->cap = 0; }
static void profile_add(Profile *p, double t, double temp) {
    if (p->count+1 > p->cap) {
        p->cap = p->cap ? p->cap*2 : 8;
        p->pts = realloc(p->pts, p->cap * sizeof(ProfilePoint));
    }
    p->pts[p->count].t = t;
    p->pts[p->count].temp = temp;
    p->count++;
}
static void profile_remove(Profile *p, size_t idx) {
    if (idx >= p->count) return;
    memmove(&p->pts[idx], &p->pts[idx+1], (p->count - idx - 1) * sizeof(ProfilePoint));
    p->count--;
}

/* ---------- Serial (Windows) ---------- */
static HANDLE serial_handle = INVALID_HANDLE_VALUE;

int serial_open(const char *dev, int baud) {
    if (serial_handle != INVALID_HANDLE_VALUE) CloseHandle(serial_handle);

    char port[20];
    if (strncmp(dev, "COM", 6) != 0) {
        snprintf(port, sizeof(port), "\\\\.\\%s", dev);
    } else {
        snprintf(port, sizeof(port), "\\\\.\\%s", dev);
    }

    serial_handle = CreateFileA(port, GENERIC_READ | GENERIC_WRITE, 0, NULL,
                               OPEN_EXISTING, FILE_ATTRIBUTE_NORMAL, NULL);

    if (serial_handle == INVALID_HANDLE_VALUE) {
        return -1;
    }

    DCB dcbSerialParams = {0};
    dcbSerialParams.DCBlength = sizeof(dcbSerialParams);

    if (!GetCommState(serial_handle, &dcbSerialParams)) {
        CloseHandle(serial_handle);
        serial_handle = INVALID_HANDLE_VALUE;
        return -1;
    }

    dcbSerialParams.BaudRate = baud;
    dcbSerialParams.ByteSize = 8;
    dcbSerialParams.StopBits = ONESTOPBIT;
    dcbSerialParams.Parity = NOPARITY;

    if (!SetCommState(serial_handle, &dcbSerialParams)) {
        CloseHandle(serial_handle);
        serial_handle = INVALID_HANDLE_VALUE;
        return -1;
    }

    COMMTIMEOUTS timeouts = {0};
    timeouts.ReadIntervalTimeout = 10;
    timeouts.ReadTotalTimeoutConstant = 10;
    timeouts.ReadTotalTimeoutMultiplier = 1;
    timeouts.WriteTotalTimeoutConstant = 50;
    timeouts.WriteTotalTimeoutMultiplier = 10;

    if (!SetCommTimeouts(serial_handle, &timeouts)) {
        CloseHandle(serial_handle);
        serial_handle = INVALID_HANDLE_VALUE;
        return -1;
    }

    return 0;
}

void serial_close_h() {
    if (serial_handle != INVALID_HANDLE_VALUE) {
        CloseHandle(serial_handle);
        serial_handle = INVALID_HANDLE_VALUE;
    }
}

ssize_t serial_write_all(const void *buf, size_t len) {
    if (serial_handle == INVALID_HANDLE_VALUE) return -1;

    DWORD bytes_written;
    if (WriteFile(serial_handle, buf, (DWORD)len, &bytes_written, NULL)) {
        return (ssize_t)bytes_written;
    }
    return -1;
}

ssize_t serial_read_some(char *buf, size_t maxlen) {
    if (serial_handle == INVALID_HANDLE_VALUE) return -1;

    DWORD bytes_read;
    if (ReadFile(serial_handle, buf, (DWORD)maxlen, &bytes_read, NULL)) {
        return (ssize_t)bytes_read;
    }
    return -1;
}

/* ---------- GUI state ---------- */
typedef struct {
    GtkWidget *window;
    GtkWidget *connect_btn;
    GtkWidget *get_status_btn;
    GtkWidget *port_entry;
    GtkWidget *log_textview;
    GtkTextBuffer *log_buf;

    GtkWidget *pid_freq_entry, *window_time_entry, *kp_entry, *ki_entry, *kd_entry;
    GtkWidget *send_pid_btn, *save_pid_btn, *get_pid_btn;

    GtkWidget *temp_label, *setpoint_label, *state_label, *time_label;

    GtkWidget *profile_canvas;
    Profile profile;

    GtkWidget *start_btn, *stop_btn;
    gboolean profile_active;
    guint profile_start_time;
    guint profile_timeout_id;
    gboolean log_serial_data;
    guint telemetry_timeout_id;
    GtkWidget *setpoint_entry;
    GtkWidget *set_setpoint_btn;
    GtkWidget *start_setpoint_btn;
    GtkWidget *stop_setpoint_btn;
    GtkWidget *time_entries[5];
    GtkWidget *temp_entries[5];
    gboolean fixed_scale;      // фиксированный масштаб
    double fixed_tmax;         // фиксированное максимальное время
    double fixed_tempmin;      // фиксированная минимальная температура
    double fixed_tempmax;      // фиксированная максимальная температура
} AppWidgets;

static AppWidgets W;

static void scroll_log_to_top(void) {
    GtkTextIter start;
    gtk_text_buffer_get_start_iter(W.log_buf, &start);
    gtk_text_view_scroll_to_iter(GTK_TEXT_VIEW(W.log_textview), &start, 0.0, FALSE, 0.0, 0.0);
}
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

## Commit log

2026-04-09 Initial commit: firmware, PC software and hardware schematics
    [MCU.SchDoc, Power.SchDoc, Termal controller.PcbDoc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]
2026-04-09 Добавлены PDF-документация из папки firmware
